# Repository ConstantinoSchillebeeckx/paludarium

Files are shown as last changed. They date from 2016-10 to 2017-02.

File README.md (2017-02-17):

:warning: this repo is no longer being worked on, the project has shifted gears to the [56gal version](https://github.com/ConstantinoSchillebeeckx/paludarium-56gal); keeping this here for historical reasons. :warning:

---

# Paludarium build
Orchid paludarium and climate control design

[Build notes](https://photoscs.wordpress.com/2016/10/26/diy-terrarium/)

## BOM

### Tank ($XX total)
- 10g aquarium ($5 craigslist)
- 4' x 2' light ceiling panel - [egg crate](https://www.google.com/shopping/product/3379815341616733842?lsf=seller:8740,store:5944499324702331793,lsfqd:0&prds=oid:14257488563428501297&q=lamp+shade&hl=en&ei=eTnxV-OXMIKFmwGgpYAQ&lsft=cm_mmc:Shopping-_-LIAs-_-D23-_-202025149&lsft=gclid:CNbavtzIvM8CFQERaQodmhcDuA) ($15 home depot)
- electric waterfall ($1 garage sale)
- [12oz great stuff foam](https://www.amazon.com/gp/product/B001AQ0FVC/ref=od_aui_detailpages00?ie=UTF8&psc=1) ($14.13 Amazon)
- [1lb. spahnum moss](https://www.amazon.com/gp/product/B00I6AJKVG/ref=od_aui_detailpages00?ie=UTF8&psc=1) ($7.99 Amazon)
- [1 x ABG mix](http://www.joshsfrogs.com/abg-mix-4-quart-1-gallon.html) ($13.98 Josh's frogs)
- [5lbs activated carbon](http://cgi.ebay.com/ws/eBayISAPI.dll?ViewItem&item=181084875793) ($9.99 ebay)
- [2lbs LECA clay](http://cgi.ebay.com/ws/eBayISAPI.dll?ViewItem&item=121695905138) ($9.45)
- [replacement pump for waterfall](http://www.newegg.com/Product/Product.aspx?Item=9SIA1GK2CA3065) ($7.99 newegg)
- [polycarbonate top 19-1/4" x 9-7/16" (1/4" thick)](http://www.tapplastics.com/product/plastics/cut_to_size_plastic/polycarbonate_sheets/516) ($13.36 TAP plastics)
- virgin cork bark
- bag of small zipties
- [PTC heater](http://www.ebay.com/itm/AC110V-100W-Electric-Ceramic-Thermostatic-Insulation-PTC-Heating-Element-Heater-/311682973018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) ($10.70 ebay)

### Flora ($XX total)
- [Davallia fejeensis](https://www.glassboxtropicals.com/ProductDetails.asp?ProductCode=Davfej)



- [Ficus pumila](https://www.glassboxtropicals.com/ProductDetails.asp?ProductCode=Ficpum)



- [Ficus pumila var. minima](https://www.glassboxtropicals.com/ProductDetails.asp?ProductCode=Ficpumminima)



- [Ficus sp. 'Panama'](https://www.glassboxtropicals.com/ProductDetails.asp?ProductCode=Ficpan)



- [Marcgravia rectiflora](https://www.glassboxtropicals.com/ProductDetails.asp?ProductCode=marcrect)



- [Pyrrosia piloselloides](https://www.glassboxtropicals.com/ProductDetails.asp?ProductCode=Pyrpil)



- [Selaginella kraussiana 'Aurea'](https://www.google.com/search?q=Selaginella+kraussiana)



- [A. capillus veneris](https://www.google.com/search?q=A.+capillus+veneris)



### Controller ($XX total)
- [2 x 50cm LED bars](http://www.ebay.com/itm/12V-36-SMD-5630-50CM-0-5M-Waterproof-LED-Hard-Strip-Bar-Light-Tube-w-Cover-Cap/232100208769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) ($4.50 ebay)
- arduino stuff
- [120mm PWM fan](http://www.newegg.com/Product/Product.aspx?Item=N82E16835494006) ($8.99 newegg)
- [temp & humidity sensor](http://www.newegg.com/Product/Product.aspx?Item=9SIABR04N71130) ($3.24 newegg)
- [ULN2003 7 Channel Darlington Driver](https://www.adafruit.com/products/970) ($1.95 Adafruit)
- [2 x 12-Channel 16-bit PWM LED Driver (TLC59711)](https://www.adafruit.com/products/1455) ($15.00 Adafruit)
- [Feather HUZZAH ESP8266](https://www.adafruit.com/products/2821) ($15.95 Adafruit)
- [Short Feather Headers](https://www.adafruit.com/products/2940) ($1.50 Adafruit)
- [UBEC DC/DC Step-Down (Buck) Converter](https://www.adafruit.com/products/1385) ($9.95 Adafruit)
- [2 x 6-conductor 0.1" socket-socket](https://www.adafruit.com/products/206) ($3.50 Adafruit)
- [Break-away 0.1" 36-pin strip right-angle male header (10 pack)](https://www.adafruit.com/products/1540) ($5.95 Adafruit)
- [4 x Servo Extension Cable](https://www.adafruit.com/products/972) ($7.80 Adafruit)
- spools of wire (1 red / 1 black)
- Schottky diode
- capacitors

### Tools
- [dremel diamond wheel point](https://www.dremel.com/en_US/products/-/show-product/accessories/7144-diamond-wheel-point) ($8.46 home depot)
- [dremel](https://www.dremel.com/en_US/products/-/show-product/tools/4000-high-performance-rotary-tool)

## Guides
- http://www.dendroboard.com/forum/members-frogs-vivariums/76255-how-build-viv-motydesign.html
- http://www.dendroboard.com/forum/members-frogs-vivariums/22002-60-gallon-construction.html
- http://www.dendroboard.com/forum/parts-construction/83431-island-paludarium-360-z-185-gal-40-x-40-x-28-a.html
- http://www.dendroboard.com/forum/parts-construction/157898-popular-helpful-parts-constructions-threads.html
- http://www.dendroboard.com/forum/parts-construction/72637-29-gallon-paludarium-build-post-i-go-details-very-pic-heavy.html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

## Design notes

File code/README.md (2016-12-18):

## Currently under development! :warning:

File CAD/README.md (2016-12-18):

# Contents

**3d_print directory**
- 3d files used for printing LED holder

**PCB**
- eagle files for custom PCB

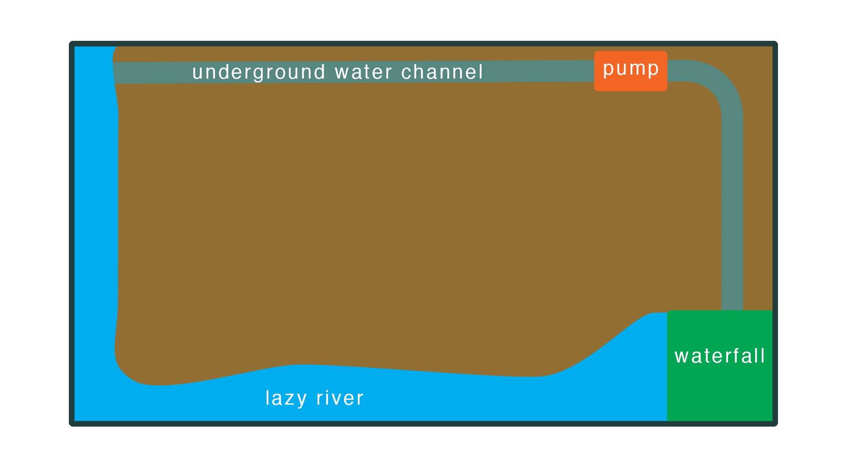
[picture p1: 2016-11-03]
figures/paludarium.png

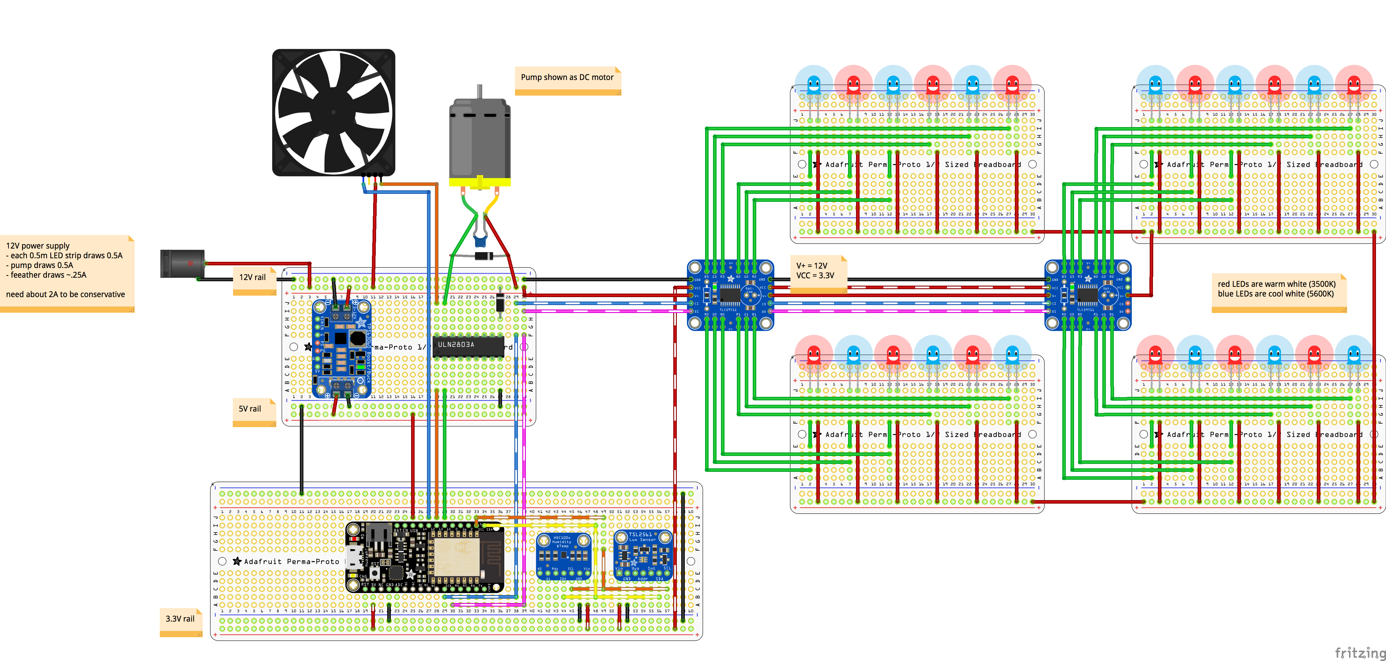
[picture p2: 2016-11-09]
figures/layout.png

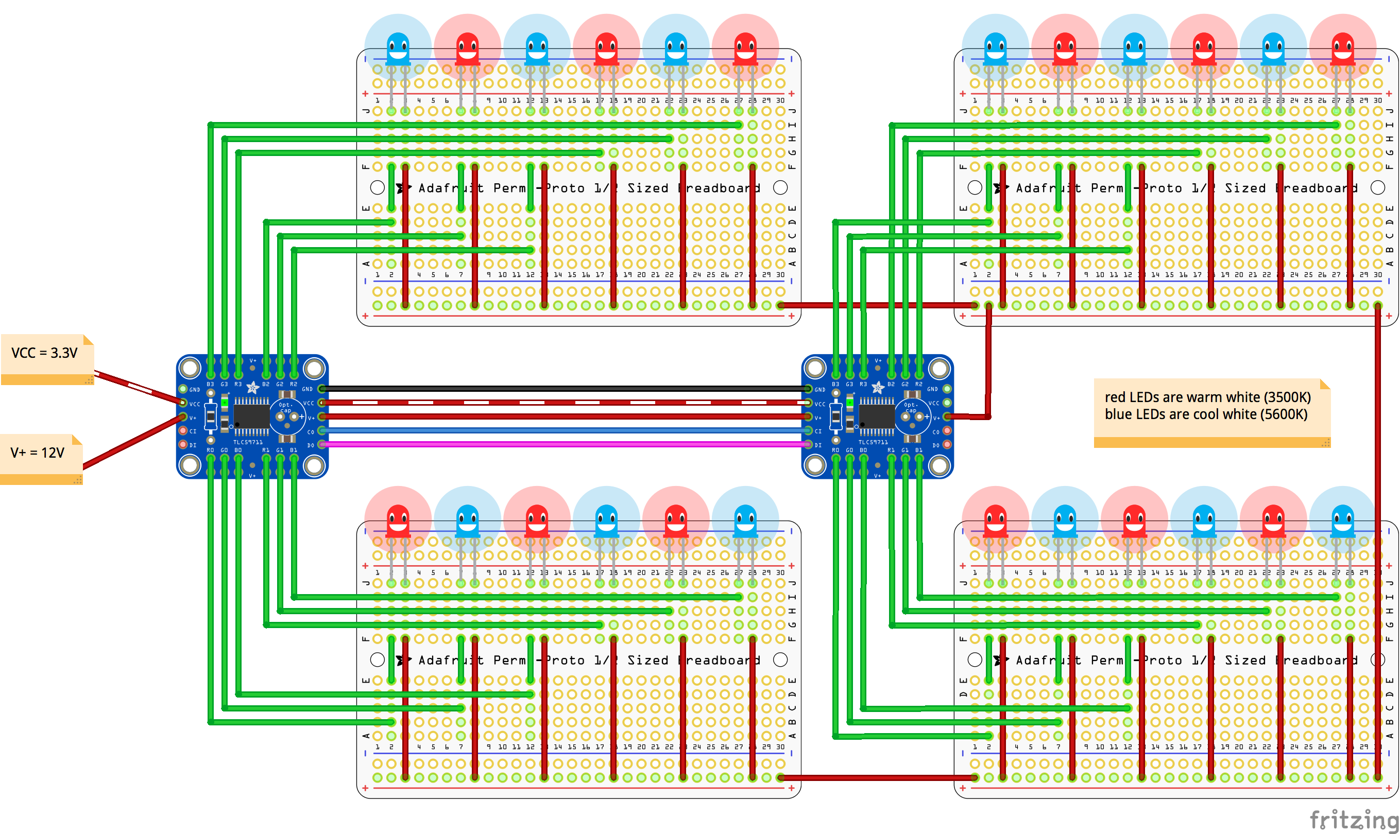
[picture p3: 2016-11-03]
figures/leds_bb.png

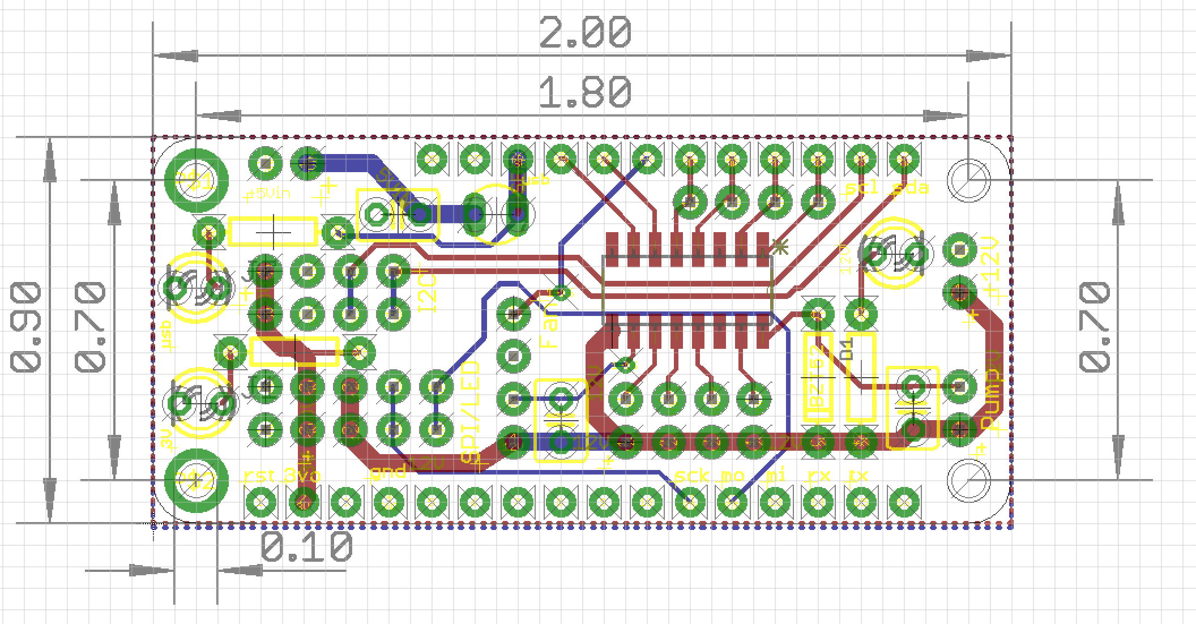
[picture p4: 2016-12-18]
CAD/PCB/PCB.png

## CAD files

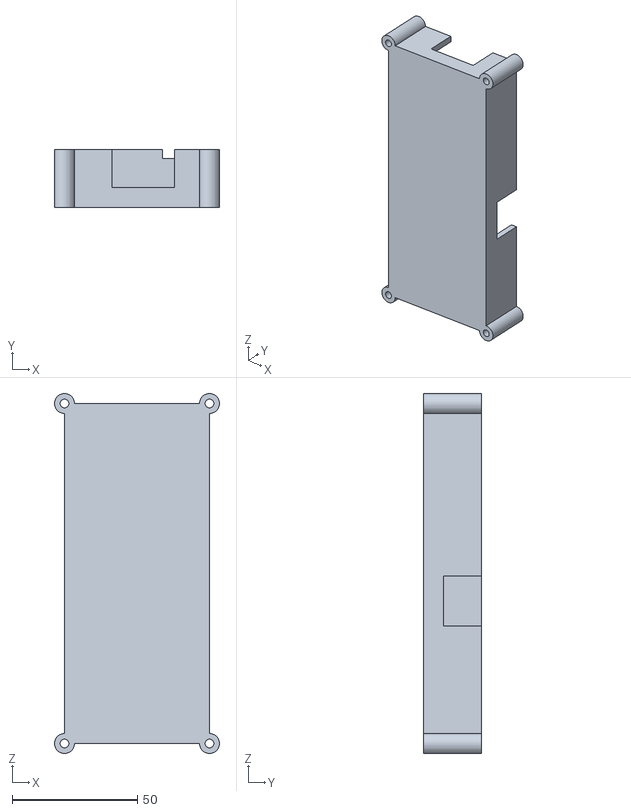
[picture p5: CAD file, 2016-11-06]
CAD/3d_print/enclosure.stl
66.0 x 23.0 x 144.0

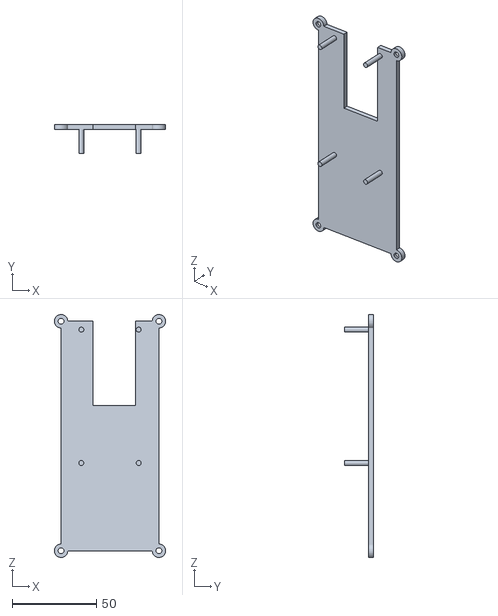
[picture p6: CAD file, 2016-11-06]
CAD/3d_print/lid.stl
66.0 x 17.0 x 144.0

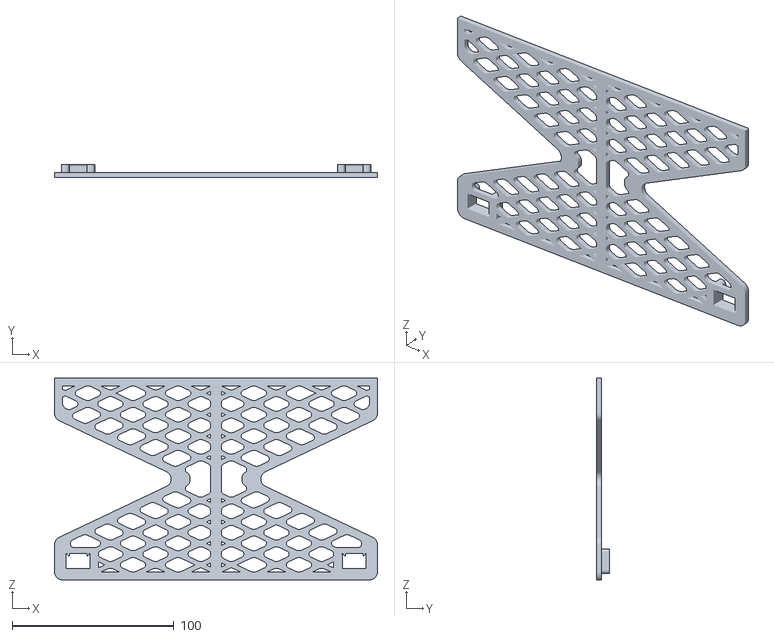
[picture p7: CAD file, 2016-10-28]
CAD/3d_print/LED_holder.stl
200.0 x 8.00 x 125.0

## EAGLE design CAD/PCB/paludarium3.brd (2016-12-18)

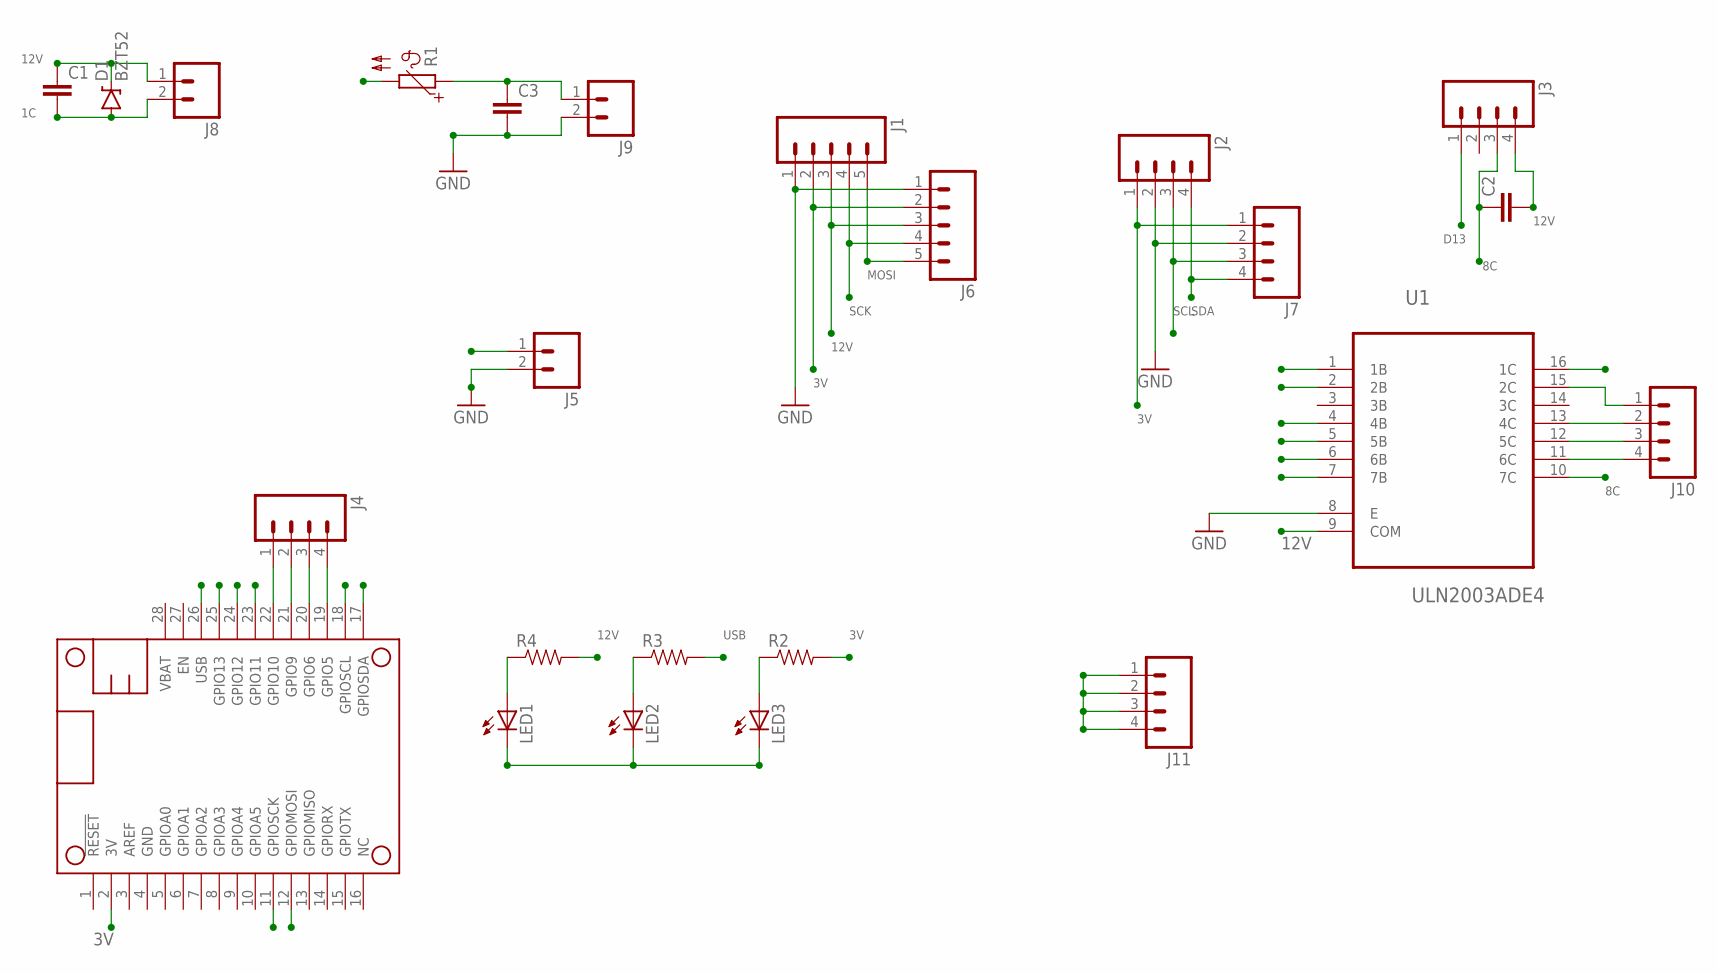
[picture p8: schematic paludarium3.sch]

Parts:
C1, C2, C3: C-EU025-030X050; C025-030X050
D1: BZT52; DIODE-BZT52
J1, J6: M05NO_SILK; 1X05_NO_SILK
J2, J3, J4, J7, J10, J11: M04NO_SILK_ALL_ROUND; 1X04_NO_SILK_ALL_ROUND
J5, J8, J9: M021X02_NO_SILK; 1X02_NO_SILK
LED1, LED2, LED3: LED3MM
MS1: FEATHERWING
R1: PTC679; P679
R2, R3, R4: RESISTORAXIAL-0.3; AXIAL-0.3
U1: ULN2003ADE4; SOIC127P600X175-16N

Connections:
1C: C1.2, D1.A, J8.2, U1.16 (1C)
3V: J1.2, J2.1, J6.2, J7.1, MS1.2 (3V), R2.P$2 (2)
5VIN: C3.1, J9.1, R1.1
8C: C2.1, J3.3, U1.10 (7C)
12V: C1.1, C2.2, D1.C, J1.3, J3.4, J5.1, J6.3, J8.1, J11.1, J11.2, J11.3, J11.4, R4.P$2 (2), U1.9 (COM)
D0: J4.2, MS1.21 (GPIO9), U1.4 (4B)
D2: J4.4, MS1.19 (GPIO5), U1.1 (1B)
D12: MS1.24 (GPIO12), U1.6 (6B)
D13: J3.1, MS1.23 (GPIO11)
D14: MS1.25 (GPIO13), U1.7 (7B)
D15: J4.1, MS1.22 (GPIO10), U1.5 (5B)
D16: J4.3, MS1.20 (GPIO6), U1.2 (2B)
GND: C3.2, J1.1, J2.2, J5.2, J6.1, J7.2, J9.2, LED1.K (C), LED2.K (C), LED3.K (C), MS1.4 (GND), U1.8 (E)
MOSI: J1.5, J6.5, MS1.12 (GPIOMOSI)
unnamed: J10.4, U1.11 (6C)
unnamed: J10.3, U1.12 (5C)
unnamed: J10.1, U1.15 (2C)
unnamed: LED1.A, R4.P$1 (1)
unnamed: J10.2, U1.13 (4C)
unnamed: LED3.A, R2.P$1 (1)
unnamed: LED2.A, R3.P$1 (1)
SCK: J1.4, J6.4, MS1.11 (GPIOSCK)
SCL: J2.3, J7.3, MS1.18 (GPIOSCL)
SDA: J2.4, J7.4, MS1.17 (GPIOSDA)
USB: MS1.26 (USB), R1.2, R3.P$2 (2)

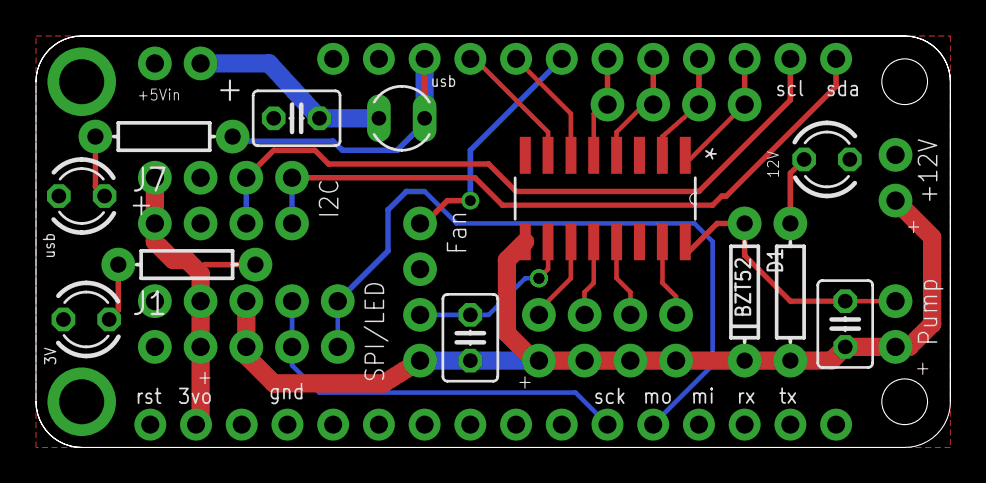
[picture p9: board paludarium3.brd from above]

Board: 2 copper layers, 50.8 x 22.9 mm, 24 parts (0 on the bottom side), 25 nets.

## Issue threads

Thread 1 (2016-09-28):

fan control

ConstantinoSchillebeeckx, 2016-09-28:
- might be able to use [this repo](https://github.com/marceloaqno/4-Wire-FAN-Arduino)
- [spec sheet](http://www.formfactors.org/developer%5Cspecs%5Crev1_2_public.pdf)

Closed 2016-11-09.

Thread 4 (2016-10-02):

To buy

ConstantinoSchillebeeckx, 2016-10-02:
- [x] driver IC for 12V pump (mosfet)
- [x] water substrate
- [x] land substrate, see https://github.com/ConstantinoSchillebeeckx/paludarium/issues/3
- [ ] flora
- [x] 1 A 30 V Schottky diode (see [here](http://electronics.stackexchange.com/questions/95140/purpose-of-the-diode-and-capacitor-in-this-motor-circuit))
- [x] [0.1 uF ceramic capacitor](https://www.adafruit.com/products/753)(see [here](http://robotics.stackexchange.com/questions/267/why-are-capacitors-added-to-motors-in-parallel-what-is-their-purpose))
- [x] moss
- [x] drift wood
- [x] [great stuff](https://www.amazon.com/dp/B001AQ0FVC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)
- [x] filtration media, see https://github.com/ConstantinoSchillebeeckx/paludarium/issues/2
- [x] light, see https://github.com/ConstantinoSchillebeeckx/paludarium/issues/5
- [x] glass top
- [x] [cork](http://www.joshsfrogs.com/backgrounds/cork-bark-flats-2.html)

Closed 2016-12-18.

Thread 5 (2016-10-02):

Light

ConstantinoSchillebeeckx, 2016-10-02:
https://www.adafruit.com/products/518

ConstantinoSchillebeeckx, 2016-10-07:
https://www.eledlights.com/led-lamps-by-type/led-tube-light-bulbs-lamps-t8-and-t12/4ft-led-tube-light-bulbs-t8-t12.html

ConstantinoSchillebeeckx, 2016-10-07:
https://www.1000bulbs.com/product/1039/FC27-FML2765.html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

ConstantinoSchillebeeckx, 2016-10-07:
could do a combo of red/blue lights, something like
- 2 x [these](http://www.bulbs.com/product/PL-S-13W-27?RefId=38)
- 2 x [these](http://www.bulbs.com/product/CF13S865?RefId=38)

ConstantinoSchillebeeckx, 2016-10-07:
hack this? https://www.amazon.com/Bioluz-LED-trade-Lumen-Dimmable/dp/B00IOWC97I

ConstantinoSchillebeeckx, 2016-10-07:
led strip
https://www.amazon.com/LEDENET%C2%AE-6500K-7000K-Bright-Aquarium-Lighting/dp/B00TZC7Y1W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
http://www.ebay.com/itm/50CM-0-5M-12V-36-SMD-5050-LED-Hard-LED-Strip-Bar-Light-w-Aluminium-Alloy-Shell/231968301261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
http://www.ebay.com/itm/5M-10X-0-5M-5630-7020-SMD-Rigid-Hard-Light-Led-Bar-Strip-Cool-Warm-White-DC-12V/371250078490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
http://www.ebay.com/itm/0-5m-2835-3014-4014-5050-5630-7020-7030-8520-Led-Strip-Rigid-Light-Bar-12V-50cm-/151943430905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

Closed 2016-10-10.

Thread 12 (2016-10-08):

microcontroller connections

ConstantinoSchillebeeckx, 2016-10-08:
- each 0.5m [led strip](http://www.ebay.com/itm/12V-36-SMD-5630-50CM-0-5M-Waterproof-LED-Hard-Strip-Bar-Light-Tube-w-Cover-Cap-/232100208769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) has 12 PCB sections , each strip is controlled by [led driver](https://www.adafruit.com/products/1455) (60mA per channel) connected through SPI (2 x digital pins).  Apparently each section only draw 0.5W (@12v = ~40mA, however it's [probably less] (http://electronics.stackexchange.com/questions/51778/large-difference-between-specced-values-and-real-values-for-led-strips)) each led strip draws 0.5W * 12 = 6W / 12V = 0.5A
- pump (12V, 5W, 0.4A) will be driven [darlington driver](https://www.adafruit.com/products/970) (1 x digital pin) - driver can sink 0.5A
- fan has PMW control built in (1 x digital)
- temp / humidity I2C (~400 uA)
- light I2C (0.5 mA max draw)

power source:
- 12V pump
- 12V led

Closed 2016-10-10.

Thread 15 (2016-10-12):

Mister

ConstantinoSchillebeeckx, 2016-10-12:
- [pump](http://www.ebay.com/itm/High-Pressure-Diaphragm-Water-Pump-With-Hose-Camping-Automatic-Switch-12v-DC-60W-/152193268405)
- [pump](http://www.ebay.com/itm/DC-12V-100PSI-4L-Min-Diaphragm-Water-Self-Priming-Pump-High-Pressure-Car-BOAT-/121954717643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)
- [nozzle](http://www.ebay.com/itm/10x-Brass-Misting-Nozzles-For-Cooling-System-0-012-0-3-mm-10-24-Garden-US-/322214820844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)
- [system](http://www.ebay.com/itm/5m-16ft-Outdoor-Garden-Misting-Cooling-System-10-Plastic-Mist-Nozzle-Sprinkler-/400952835348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)

Closed 2016-12-18.

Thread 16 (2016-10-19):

Build notes

ConstantinoSchillebeeckx, 2016-10-19:
- [x] Add screen mesh in the bottom of the back filter channel
- [x] Add a tube to the pump inlet so that the inlet is extended to the middle of the charcoal (away from the waterfall) add a mesh cover for the tube inlet
- [x] Add foam around the base of the water fall (create lip so water all falls in front)
- [x] Obstruct water flow from waterfall short-path to pump
- [x] Add foam splash guard at the top of the water fall
- [x] Add weight in the corner opposite of the pump - will raise with foam & water (maybe add rocks on the inside/under the false bottom

Closed 2016-10-23.

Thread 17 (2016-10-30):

plants

ConstantinoSchillebeeckx, 2016-10-30:
http://www.glassboxtropicals.com/

**Vines**
- [marcgravia rectiflora](https://www.google.com/search?q=marcgravia+rectiflora)
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
- [Microgramma vacciniifolia](https://www.google.com/search?q=Microgramma+vacciniifolia)
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

- [Ficus pumila var. quercifolia](https://www.google.com/search?q=Ficus+pumila+var.+quercifolia)
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

- [ficus pumila](https://www.google.com/search?q=Ficus+pumila)
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

- [Ficus Borneo](https://www.google.com/search?q=ficus+borneo)
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

- Marcgravia sintenisii

- [Pyrrosia Piloselloides](http://www.glassboxtropicals.com/Pyrrosia-piloselloides-p/pyrpil.htm)
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

- [moss fern - Selaginella pallescens](https://www.google.com/search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)
- [sundew](https://www.google.com/search?q=sundew)
- maidenhair fern
- fittonia

ConstantinoSchillebeeckx, 2016-11-14:
purchase of various vines and an orchid:
[glassbox_receipt.pdf](https://github.com/ConstantinoSchillebeeckx/paludarium/files/590624/glassbox_receipt.pdf)

Closed 2016-12-18.

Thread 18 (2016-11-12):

motor noise

ConstantinoSchillebeeckx, 2016-11-12:
http://www.thebox.myzen.co.uk/Tutorial/De-coupling.html

Closed 2016-12-18.

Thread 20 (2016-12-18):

finalize holes need on end plates

ConstantinoSchillebeeckx, 2016-12-18:
**bottom**
- bulkhead for filter inlet (e.g. [this](http://www.mistking.com/3-4-Drain-Bulkhead-Slip-Kit.html) or [this](https://www.amazon.com/Lifegard-Aquatics-Bulkhead-Fitting-Kit/dp/B002DVWOIA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))
- wiring for heaters

**top**
- fan
- wires for LEDS
- tubes for rain
- wires for sensors

**other**
- return line from filter
- stabilizing rods

Closed 2016-12-18.

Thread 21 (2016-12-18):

plumbing

ConstantinoSchillebeeckx, 2016-12-18:
[valve](https://www.amazon.com/Two-Little-Fishies-ATL5445W-Regulating/dp/B00025675K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)
[bulkhead](https://www.amazon.com/Lifegard-Aquatics-Bulkhead-Fitting-Kit/dp/B002DVWOIA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)
[tubing](https://www.amazon.com/TotalPond-V16010-Vinyl-Tubing/dp/B004DL0Y9O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)
[pump](https://www.amazon.com/Uniclife-Brushless-Water-Pump-Submersible/dp/B01DWCPFUC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)
[solenoid valve](https://www.adafruit.com/products/997?gclid=CN3VyKqh_tACFRC2wAodkKoMLw)

Closed 2016-12-18.

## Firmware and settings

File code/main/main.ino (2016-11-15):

#include "Adafruit_TLC59711.h"
#include <SPI.h>
#include <ESP8266WiFi.h>
#include "Adafruit_MQTT.h"
#include "Adafruit_MQTT_Client.h"
#include <Adafruit_SSD1306.h>

#include <Wire.h>
#include <Adafruit_Sensor.h>
#include <Adafruit_TSL2561_U.h>
#include "Adafruit_Si7021.h"



#define data   13 // MO(SI)
#define clock  14 // SCK

#define numStrip 2

/************************* WiFi Access Point *********************************/

#define WLAN_SSID       "interpol"
#define WLAN_PASS       "schillebeeckx"

/************************* Adafruit.io Setup *********************************/

#define AIO_SERVER      "io.adafruit.com"
#define AIO_SERVERPORT  1883                   // use 8883 for SSL
#define AIO_USERNAME    "constantinoschillebeeckx"
#define AIO_KEY         "f40d869993b5cc6315c96943bf7d005e4246fc86"

Adafruit_TLC59711 led = Adafruit_TLC59711(numStrip, clock, data); // LED driver
Adafruit_SSD1306 display = Adafruit_SSD1306(); // OLED display
//Adafruit_TSL2561_Unified lux = Adafruit_TSL2561_Unified(TSL2561_ADDR_FLOAT, 12345); // light sensor
Adafruit_Si7021 sensor = Adafruit_Si7021(); // temp & humidity

// Calculate based on max input size expected for one command
#define INPUT_SIZE 7  // max is L:65535 -> 7

#define BUTTON_A 0
#define BUTTON_B 16
#define BUTTON_C 2
#define LED      0

// Create an ESP8266 WiFiClient class to connect to the MQTT server.
WiFiClient client;

// Setup the MQTT client class by passing in the WiFi client and MQTT server and login details.
Adafruit_MQTT_Client mqtt(&client, AIO_SERVER, AIO_SERVERPORT, AIO_USERNAME, AIO_KEY);

// Setup a feed for publishing.
// Notice MQTT paths for AIO follow the form: <username>/feeds/<feedname>
Adafruit_MQTT_Publish tempMQTT = Adafruit_MQTT_Publish(&mqtt, AIO_USERNAME "/feeds/temp");
Adafruit_MQTT_Publish humidMQTT = Adafruit_MQTT_Publish(&mqtt, AIO_USERNAME "/feeds/humidity");


#if defined(ARDUINO_ARCH_SAMD)
// for Zero, output on USB Serial console, remove line below if using programming port to program the Zero!
   #define Serial SerialUSB
#endif



unsigned long previousMillis = 0;   
const long interval = 15 * 60 * 1000; // 15 min

uint32_t temp=0;
uint32_t humid=0;
uint32_t prevTemp=0;
uint32_t prevHumid=0;
//uint32_t lum=0;

byte pumpPin = 15;
byte fanOnOff = 13;
byte fanPWM = 12;


#if (SSD1306_LCDHEIGHT != 32)
#error("Height incorrect, please fix Adafruit_SSD1306.h!");
#endif

void setup() {

  #if !defined(ESP8266)
    while (!Serial) delay(1);
  #endif
  
  Serial.begin(115200);

  display.begin(SSD1306_SWITCHCAPVCC, 0x3C);  // initialize with the I2C addr 0x3C (for the 128x32)
  // Clear the buffer.
  display.clearDisplay();
  display.display();
  display.setTextSize(1);
  display.setTextColor(WHITE);
  display.setCursor(0,0);


  pinMode(pumpPin, OUTPUT);
  analogWrite(pumpPin, 0);
  pinMode(fanOnOff, OUTPUT);
  analogWrite(fanOnOff, 0);
  pinMode(fanPWM, OUTPUT);
  analogWrite(fanPWM, 0);
  delay(10);

  // Connect to WiFi access point.
  Serial.println(); Serial.println();
  Serial.print("Connecting to ");
  Serial.println(WLAN_SSID);
  display.println("Connecting to: ");
  display.println(WLAN_SSID);
  yield();
  display.display();

  WiFi.begin(WLAN_SSID, WLAN_PASS);
  while (WiFi.status() != WL_CONNECTED) {
    delay(500);
    Serial.print(".");
  }
  Serial.println();

  Serial.println("WiFi connected");
  Serial.println("IP address: "); Serial.println(WiFi.localIP());
    

  if (!sensor.begin()) {
    Serial.println("Couldn't find sensor!");
    while (1);
  }
  
  /* Setup the sensor gain and integration time */
//  configureSensor();
  
  led.begin();
  led.write();

  // get initial reading
  temp = sensor.readTemperature() * 9.0/5 + 32;
  humid = sensor.readHumidity();
}

void loop() {

  delay(1000);
  unsigned long currentMillis = millis();

  // Ensure the connection to the MQTT server is alive (this will make the first
  // connection and automatically reconnect when disconnected).  
  MQTT_connect();

  temp = sensor.readTemperature() * 9.0/5 + 32;
  humid = sensor.readHumidity();

  if (abs(currentMillis - previousMillis) >= interval) {
    // save the last time you blinked the LED
    previousMillis = currentMillis;
    
    Serial.print(temp);
    Serial.print(" ");
    Serial.println(humid);
    
    tempMQTT.publish(temp);
    humidMQTT.publish(humid);

  }


  // keep the connection alive
  mqtt.ping();


  // update display if temp/humidity has changed
  if (prevHumid != humid || prevTemp != temp) {
    display.clearDisplay();
    display.display();
    display.setCursor(0,0);
    display.print("Temp: ");
    display.println(temp);
    display.print("Humidity: ");
    display.println(humid);
    yield();
    display.display();
  }
  prevHumid = humid;
  prevTemp = temp;




  // PARSE COMMANDS ON SERIAL
  parseSerialComm();

  
}

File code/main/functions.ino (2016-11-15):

void parseSerialComm() {
  // Get next command from Serial (add 1 for final 0)
  char input[INPUT_SIZE + 1];
  byte size = Serial.readBytes(input, INPUT_SIZE);
  
  // Add the final 0 to end the C string
  input[size] = 0;

  // Read each command pair, split on ':'
  // e.g. L:65535
  // L -> LED
  // P -> pump
  // F -> fan
  char* tok = strtok(input, ":");
  while (tok != NULL) {

    if (strchr(tok, 'L')) { // LED COMMANDS
      Serial.print("LED command: ");
      tok = strtok(NULL, ":"); // get next token
      
      long val = atoi(tok);
      Serial.println(val);
      setLED(val);
    } else if (strchr(tok, 'P')) { // PUMP COMMANDS
      Serial.print("Pump command: ");
      tok = strtok(NULL, ":"); // get next token
      
      long val = atoi(tok);
 
      if (val >= 0 && val <= 1023) {
        analogWrite(pumpPin, 1023);
        delay(100);
        analogWrite(pumpPin, val);
        Serial.println(val);
      }
    } else if (strchr(tok, 'F')) { // FAN COMMANDS
      Serial.print("Fan command: ");
      tok = strtok(NULL, ":"); // get next token

      long val = atoi(tok);
 
      if (val >= 0 && val <= 1023) {
        analogWrite(fanPWM, val);
        analogWrite(fanOnOff, val == 0 ? 0 : 1023);
        Serial.println(val);
      }
    }
    
    tok = strtok(NULL, ":"); // get next token
  }

}


/*
 * Set all LED sections to given brigthness i
 * (max 65535)
 */
void setLED(long i) {
   if (i >= 0 && i <= 65535) {
    for (byte j = 0; j <= 7; j++) {
      led.setLED(j, i, i, i);
      led.write();
    }
  }
}







/*
 * Set LED section brigthness.
 * NOTE: all other LEDs will be
 * turned off.
 * 
 * Params:
 * -------
 * i - index for LED section (1 to 24)
 * val - brigthness value (0 to 65535
 * 
 */
void setLEDSection(byte i, long val) {
  
  // bottom LED strip
  led.setLED(0, val * (i == 8), val * (i == 4), val * (i == 6));
  led.write();
  led.setLED(1, val * (i == 9), val * (i == 12), val * (i == 5));
  led.write();
  led.setLED(2, val * (i == 7), val * (i == 10), val * (i == 3));
  led.write();
  led.setLED(3, val * (i == 11), val * (i == 1), val * (i == 2));
  led.write();


  // top LED strip
  led.setLED(4, val * (i == 23), val * (i == 14), val * (i == 18));
  led.write();
  led.setLED(5, val * (i == 19), val * (i == 20), val * (i == 21));
  led.write();
  led.setLED(6, val * (i == 17), val * (i == 16), val * (i == 22));
  led.write();
  led.setLED(7, val * (i == 13), val * (i == 15), val * (i == 24));
  led.write();
  
}





// Function to connect and reconnect as necessary to the MQTT server.
// Should be called in the loop function and it will take care if connecting.
void MQTT_connect() {
  int8_t ret;

  // Stop if already connected.
  if (mqtt.connected()) {
    return;
  }

  Serial.print("Connecting to MQTT... ");

  uint8_t retries = 3;
  while ((ret = mqtt.connect()) != 0) { // connect will return 0 for connected
       Serial.println(mqtt.connectErrorString(ret));
       Serial.println("Retrying MQTT connection in 60 seconds...");
       mqtt.disconnect();
       delay(60000);  // wait 60 seconds
       retries--;
       if (retries == 0) {
         // basically die and wait for WDT to reset me
         while (1);
       }
  }
  Serial.println("MQTT Connected!");
}

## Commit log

2016-10-02 updated BOM
2016-11-03 code, figures, gitignore
    [layout.fzz, leds.fzz]
2016-11-06 added CAD for enclosure
    [LED_holder.stl, enclosure.stl, lid.stl]
2016-11-06 update FAN control to ULN2803
    [layout.fzz]
2016-11-15 code cleanup
    [layout.fzz]

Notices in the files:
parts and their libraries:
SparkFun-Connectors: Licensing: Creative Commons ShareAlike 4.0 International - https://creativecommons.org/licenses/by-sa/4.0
